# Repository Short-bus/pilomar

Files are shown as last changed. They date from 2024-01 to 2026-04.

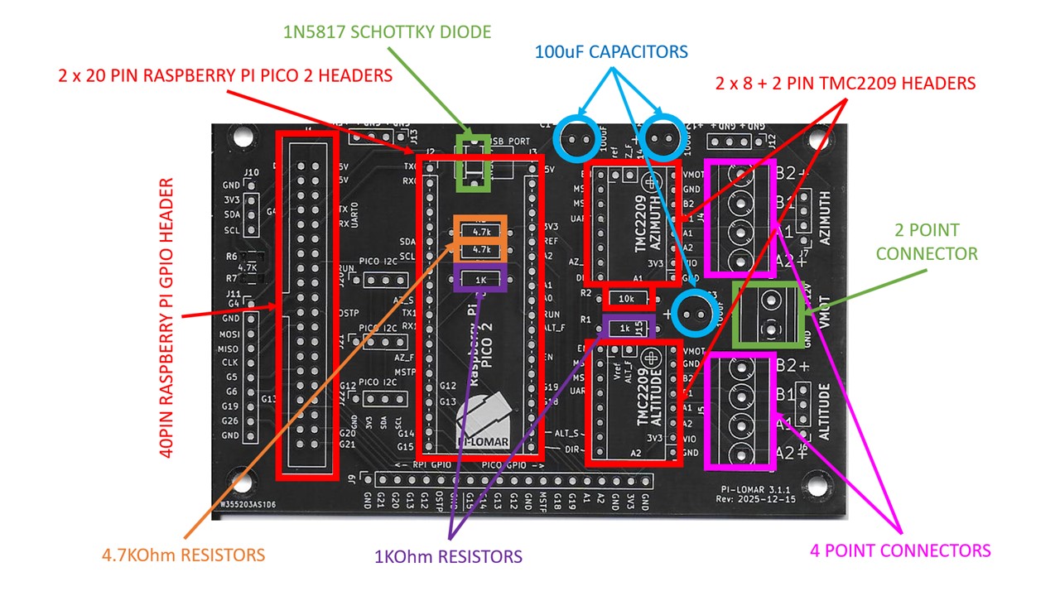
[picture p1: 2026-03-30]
gerber/PCB-2025-12-15/PCB GUIDE 2025-12-15.jpg

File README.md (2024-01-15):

# pi-lomar
RaspberryPi based miniature observatory.
A Python3 project to control a small camera and telephoto lens housed in a miniature 3D printed observatory enclosure.
This combines multiple open modules to handle object location, tracking and image capture.

This uses Python3 on the Raspberry Pi and CircuitPython on a connected Pimoroni Tiny2040 microcontroller.

The physical telescope, mechanism and dome is buildable from the Instructables page.
[https://www.instructables.com/Pi-lomar-3D-Printed-Working-Miniature-Observatory-/]

The wiki for pi-lomar is here.
[https://github.com/Short-bus/pilomar/wiki]

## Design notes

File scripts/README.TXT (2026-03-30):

This folder contains scripts for building the Pilomar project.

buildpilomar is the original (now deprecated build script).
buildpilomar_buster32 is the script to build on BUSTER O/S (for RPi3B and RPi4B).
buildpilomar_bookworm64 is the script to build on BOOKWORM O/S (for RPI4B and RPI5B).
zip-pilomar is a backup script. It archives the main programs and data files for pilomar.
astrometry.net will install the astrometry.net plate solving package on the RPi. It includes the asterism data files appropriate for the 16-50mm lenses used by the project.

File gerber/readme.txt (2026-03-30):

Each folder in the gerber directory is a complete Gerber file set for a single PCB design.

To send the Gerber files for manufacturing you should select the PCB version you want and ZIP all the files in that folder.
Eg:
  cd gerber/PCB-2023-12-14
  zip PCB-2023-12-14.zip *

Please order the board UNPOPULATED, the GERBER files do not specify the components, you need to add those manually when you 
have received the unpopulated PCBs.

These designs are made in good faith and are best efforts, but no guarantees are provided. 
Please be sure you are happy with their function and safety before using in your project.

PCB designs ----------------------------------------------------------------------------------------------------------------

PCB-2023-12-14 
  This is the initial PCB design for the motorcontrol board.
  Microcontroller: Pimoroni Tiny2040 and Tiny2350
  Stepper driver: DRV8815

PCB-2025-12-15
  This is the V3.1.1 version of the motorcontrol board.
  Microcontroller: Raspberry Pi Pico 2 (NOT PICO 1)
  Stepper driver: TMC2209 (Recommend Big Tree Tech V1.3)

Manufacturing settings -----------------------------------------------------------------------------------------------------

Board type : Single pieces
Different design in panel： 1
Size : 111.9 x 72.5 mm
Quantity :5
Layer : 2 Layers
Material :FR-4: TG130
Thickness : 1.6 mm
Min track/spacing : 8/8mil
Min hole size : 0.3mm ↑
Solder mask : Purple
Silkscreen : White
Edge connector : No
Surface finish : HASL with lead
"HASL" to "ENIG" : No
Via process : Tenting vias
Finished copper : 1 oz Cu
Remove product No. : No
Customized Services and Advanced Options : UL marking:None,

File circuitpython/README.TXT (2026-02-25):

This folder contains circuitpython code for the Pilomar project.

The tiny2040 subfolder contains the code.py program on the following setup:
    Pimoroni Tiny2040 microcontroller. 
    CircuitPython 7.2 to 8.2 only.
    drv8825 stepper motor drivers only.

The tiny2350 subfolder contains the code.py program on the following setup:
    Pimoroni Tiny2350 microcontroller. 
    CircuitPython 9.2 or later with RP2350 support.
    drv8825 stepper motor drivers only.

The pico2_tmc2209 subfolder contains the code.py program on the following setup:
    Raspberry Pi Pico2 microcontroller.
    CircuitPython 9.2 or later with Pico2 RP2350 support.
    tmc2209 stepper motor drivers only.

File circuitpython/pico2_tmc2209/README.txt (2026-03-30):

Files for:
   RASPBERRY PI PICO2 WITH TMC2209 STEPPER DRIVERS.
   These files are not designed to work on other microcontrollers or different stepper drivers.

This requires a circuit based upon the V3.1.1 motorcontroller because the microcontroller and stepper drivers have changed!

pi/circuitpython/pico2_tmc2209
│  
├─ README.txt # This file.
│  
├─ code.py # Primary program to run on Pico2 with tmc2209 stepper drivers.
│  
├─ tmc2209.py # Generic TMC Stepper library for communicating with tmc2209 stepper driver.
│  
├─ erase.py # Example code to erase file system on pico2 if a reset is needed.
│  
├─ as5600.py # Generic as5600 library for communicating with as5600 sensors.
│  
├─ pilomar # Pilomar project specific libraries.
│  │  
│  ├─ devices.py # Wrappers for sensors so they present common features to the project.
│  │  
│  ├─ enum.py # Used by some libraries.
│  │  
│  ├─ helpers.py # Misc functions and minor classes used by project.
│  │  
│  ├─ steppermotor.py # Main stepper motor class for the project.
│  │  
│  ├─ trajectory.py # Trajectory related classes for the project.
│  │  
│  └─ uarthost.py # UART serial communication handler for the project.
│
└─ lib # Adafruit libraries, included in project for convenience.
   │  
   ├─ adafruit_bus_device # Copy of adafruit_bus_device folder for convenience.
   │  
   ├─ adafruit_register # Copy of adafruit_register folder for convenience.
   │  
   └─ adafruit_lis3dh.mpy # Adafruit lis3dh handler included for convenience.

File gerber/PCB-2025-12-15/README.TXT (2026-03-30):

Gerber files to produce V3.1.1 PCB for the project.
This the newer PCB design which uses Raspberry Pi Pico2 microcontroller and TMC2209 stepper drivers.

You need to provide the following components to complete the board.
1 x 40 pin Raspberry Pi GPIO header.
2 x 20 pin headers for Raspberry Pi PICO2.
4 x 8 pin headers for TMC2209 drivers.
2 x 2 pin headers for TMC2209 drivers (NOTE: 2 extra pins along top edge of driver board).
2 x TMC2209 driver boards (recommend BigTreeTech V1.3 or equivalent).
1 x Raspberry Pi PICO2 microcontroller (NOTE: PICO1 does not work).
1 x 1N5817 Schottky diode.
2 x 4.7K resistors.
2 x 1.0K resistors.
1 x 10K resistor.
2 x 4 point terminal block.
1 x 2 point terminal block.
3 x 100uF Capacitors.

This requires software released from 2026 onwards. Earlier versions of Pilomar will not communicate correctly with this design.

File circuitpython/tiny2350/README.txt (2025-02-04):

This contains the circuitpython code for the Pimoroni Tiny2350 microcontroller.

To install:
1) Install CircuitPython on the Tiny2350. Version 9.2 works OK. Earlier versions do not support the Tiny2350 fully.
2) Copy code.py from this folder onto the Tiny2350.
3) Restart the Tiny2350.

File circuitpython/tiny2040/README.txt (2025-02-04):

This contains the circuitpython code for the Pimoroni Tiny2040 microcontroller.

To install:
1) Install CircuitPython on the Tiny2040. Versions 7.2 and 8.2 work OK. Later versions do not, they are too large.
2) Copy code.py from this folder onto the Tiny2040.
3) Restart the Tiny2040.

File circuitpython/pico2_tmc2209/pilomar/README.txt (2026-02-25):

circuitpython helper libraries for pico2 & tmc2209 support.

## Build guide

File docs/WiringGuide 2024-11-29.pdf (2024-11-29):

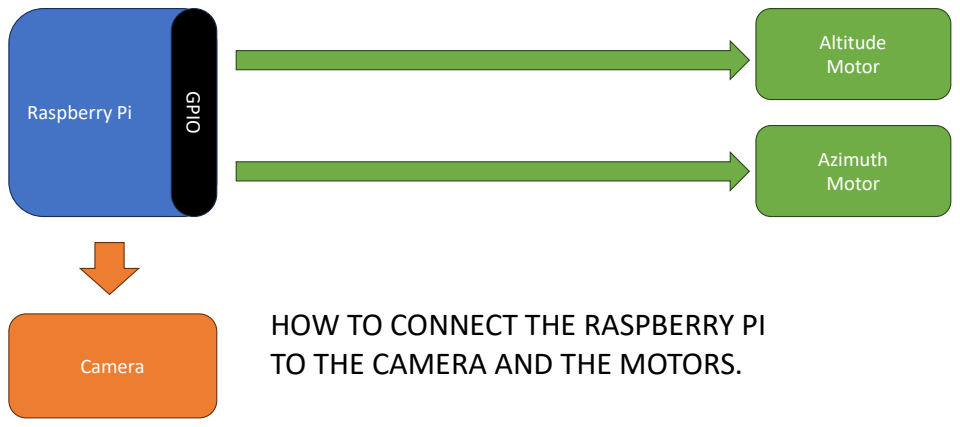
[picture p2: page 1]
Raspberry Pi; Altitude Motor; Camera; Azimuth; Motor GPIO

HOW TO CONNECT THE RASPBERRY PI
TO THE CAMERA AND THE MOTORS.

IDEALLY THE RASPBERRY PI WOULD
DIRECTLY CONTROL THE STEPPER
MOTORS THROUGH THE GPIO PORTS

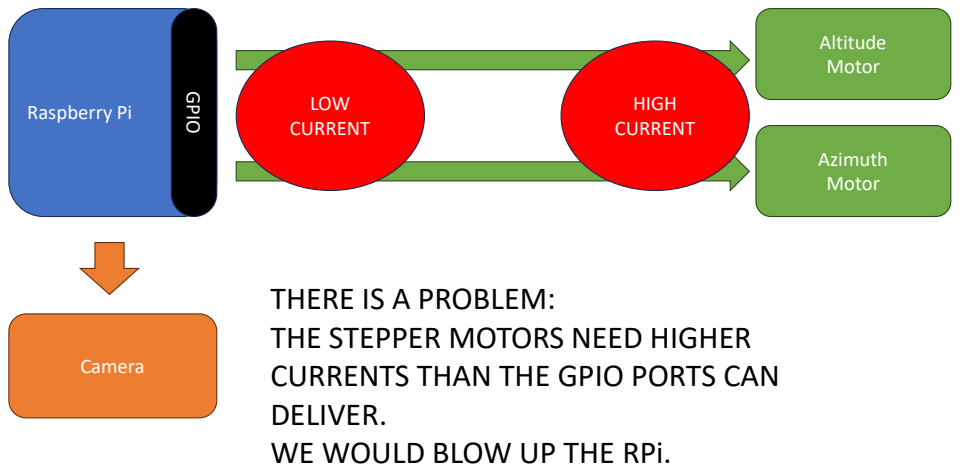
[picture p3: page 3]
Raspberry Pi; Altitude Motor; Camera; Azimuth; Motor GPIO; HIGH; CURRENT; LOW CURRENT

THERE IS A PROBLEM:
THE STEPPER MOTORS NEED HIGHER
CURRENTS THAN THE GPIO PORTS CAN
DELIVER.
WE WOULD BLOW UP THE RPi.

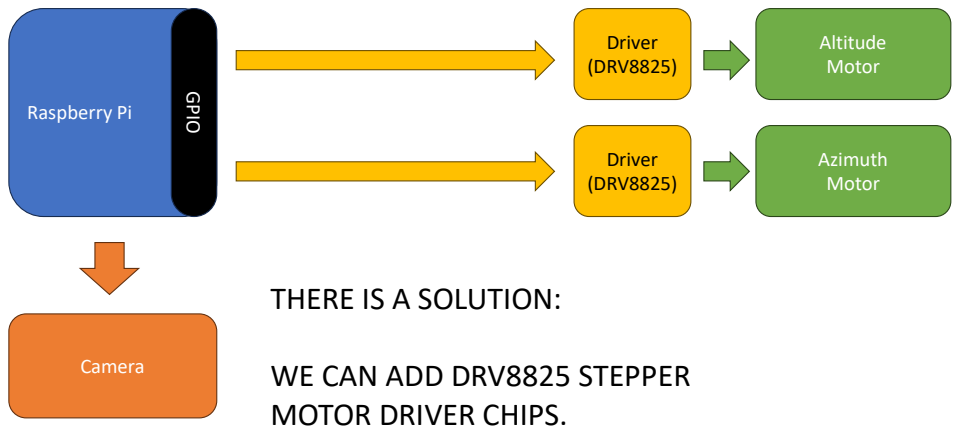
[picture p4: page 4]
Raspberry Pi; Altitude Motor; Camera; Driver (DRV8825); Azimuth Motor; Driver; (DRV8825) GPIO

THERE IS A SOLUTION:

WE CAN ADD DRV8825 STEPPER
MOTOR DRIVER CHIPS.

DRV8825 TAKES LOW POWER SIGNALS FROM
PROCESSORS TO CONTROL HIGHER
CURRENT/VOLTAGE POWER DIRECTLY TO THE
STEPPER MOTORS.

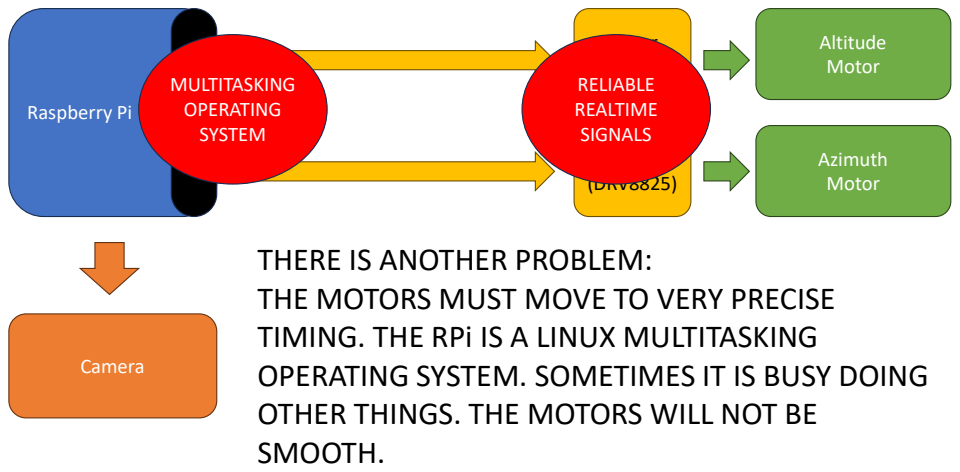
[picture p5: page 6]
Raspberry Pi; Altitude Motor; Camera; Driver (DRV8825); Azimuth Motor; Driver; (DRV8825) GPIO; RELIABLE REALTIME SIGNALS; MULTITASKING OPERATING SYSTEM

THERE IS ANOTHER PROBLEM:
THE MOTORS MUST MOVE TO VERY PRECISE
TIMING. THE RPi IS A LINUX MULTITASKING
OPERATING SYSTEM. SOMETIMES IT IS BUSY DOING
OTHER THINGS. THE MOTORS WILL NOT BE
SMOOTH.

THERE IS A SOLUTION:

INSERT A MICROCONTROLLER WHICH CAN PROVIDE
RELIABLE SIGNALS TO THE MOTORS. EVEN IF THE RPi
IS BUSY!

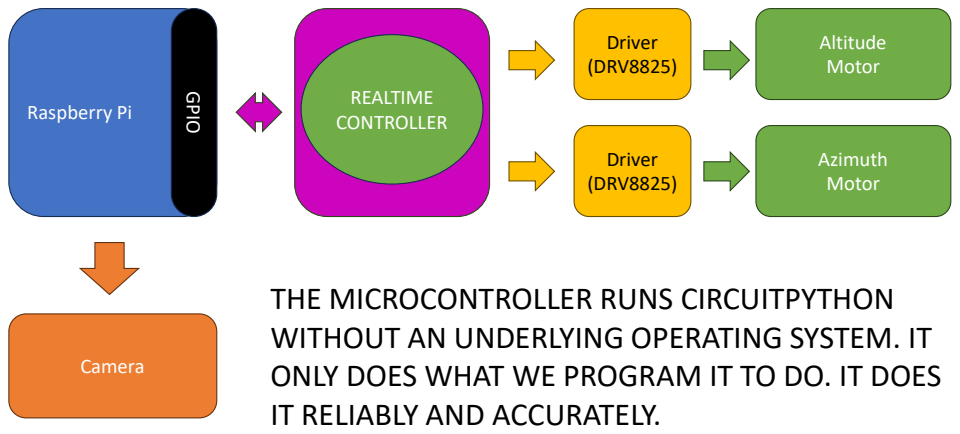
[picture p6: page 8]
Raspberry Pi; Altitude Motor; Camera; Driver (DRV8825); Microcontroller; Azimuth Motor; Driver; (DRV8825) GPIO; REALTIME; CONTROLLER

THE MICROCONTROLLER RUNS CIRCUITPYTHON
WITHOUT AN UNDERLYING OPERATING SYSTEM. IT
ONLY DOES WHAT WE PROGRAM IT TO DO. IT DOES
IT RELIABLY AND ACCURATELY.

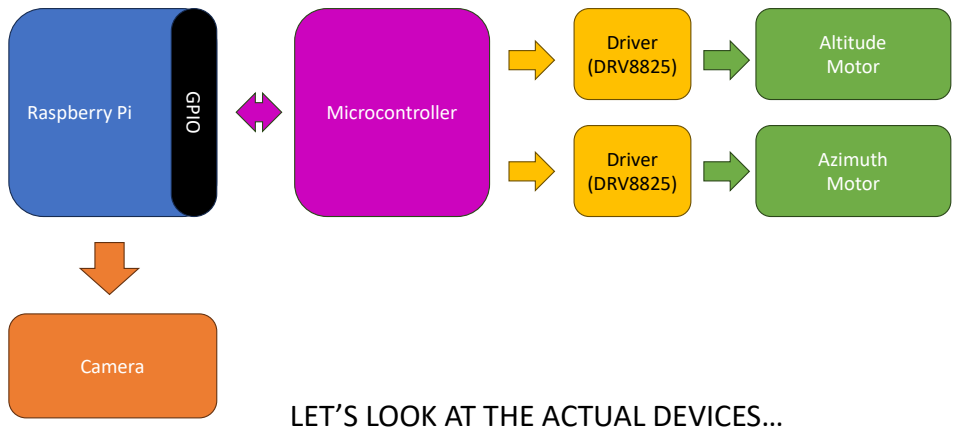
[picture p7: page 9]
Raspberry Pi; Altitude Motor; Camera; Driver (DRV8825); Microcontroller; Azimuth Motor; Driver; (DRV8825) GPIO

LET’S LOOK AT THE ACTUAL DEVICES…

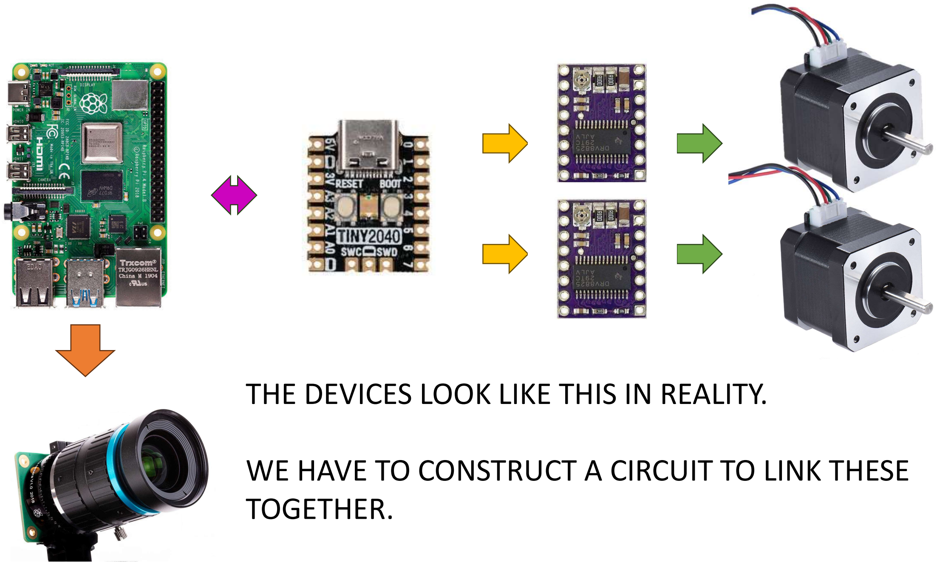
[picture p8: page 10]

THE DEVICES LOOK LIKE THIS IN REALITY.

# WE HAVE TO CONSTRUCT A CIRCUIT TO LINK THESE

TOGETHER.

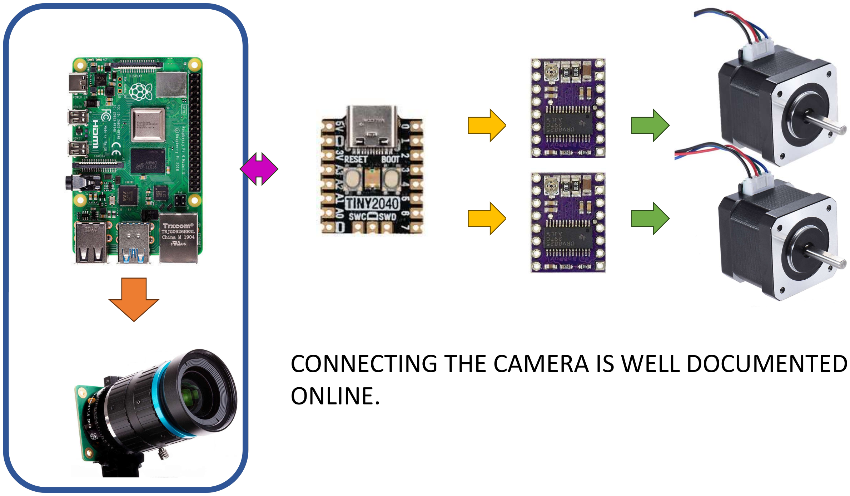
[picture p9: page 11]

# CONNECTING THE CAMERA IS WELL DOCUMENTED

ONLINE.

WE DON’T NEED TO DO ANYTHING SPECIAL WITH
THE CAMERA. JUST CONNECT IT AS EXPECTED.

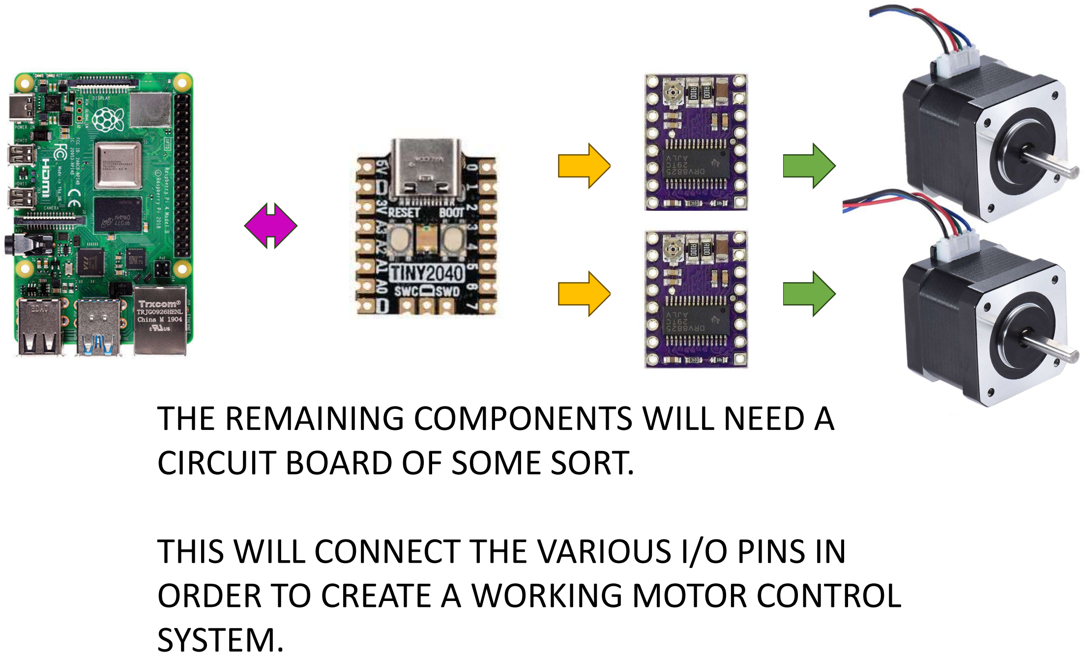
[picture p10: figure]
THE REMAINING COMPONENTS WILL NEED A CIRCUIT BOARD OF SOME SORT.; ORDER TO CREATE A WORKING MOTOR CONTROL SYSTEM.

# THIS WILL CONNECT THE VARIOUS I/O PINS IN

## RPI GPIO

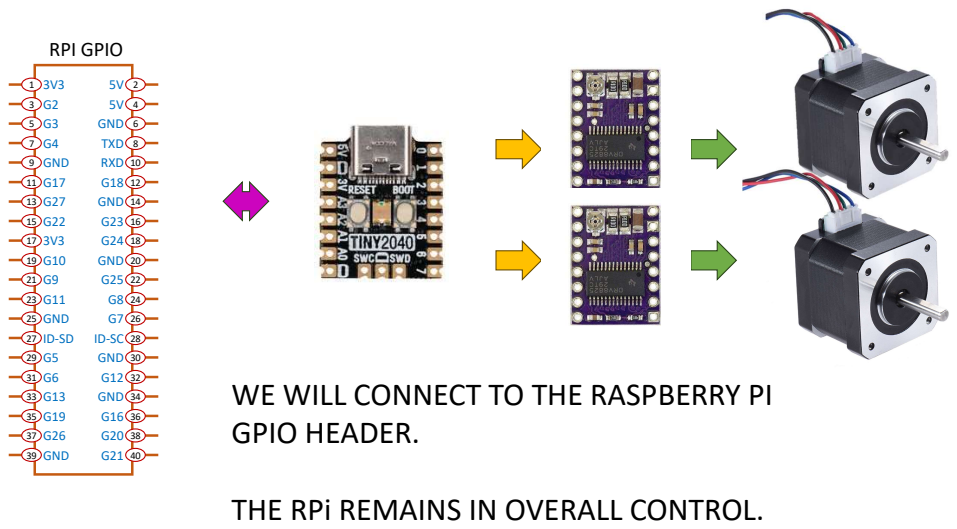
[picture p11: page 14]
5V 5V GND TXD RXD G18 GND G23 G24 GND; G8 G7 ID-SC GND G12 GND G16 G20 G21; 3V3 G2 G3 G4 GND G17 G27 G22 3V3 G10; G11 GND; G5 G6 G13 G19 G26 GND; WE WILL CONNECT TO THE RASPBERRY PI GPIO HEADER.; THE RPi REMAINS IN OVERALL CONTROL.

## TINY2040

## RPI GPIO

## TINY2040

# ID-SD ¹³⁵⁷⁹

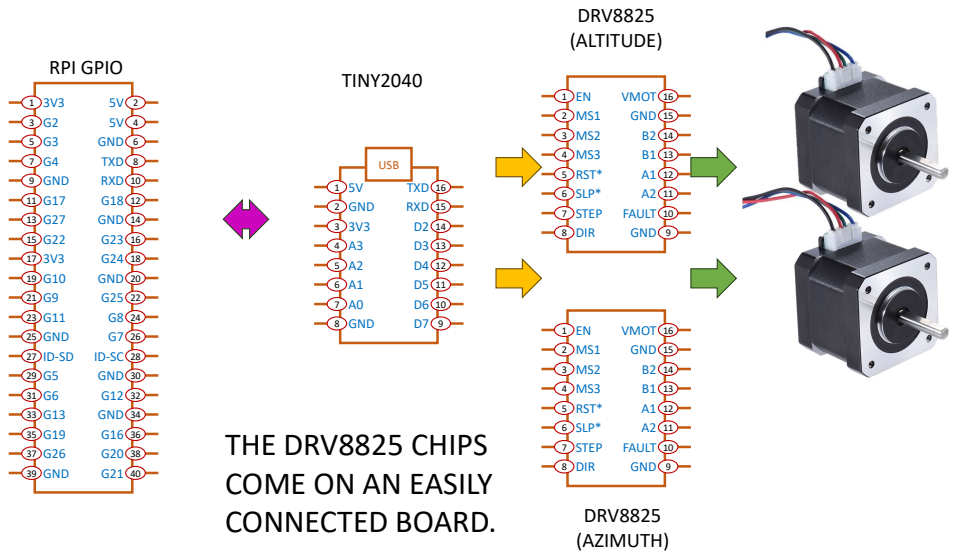
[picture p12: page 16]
5V 5V GND TXD RXD G18 GND G23 G24 GND; G8 G7 ID-SC GND G12 GND G16 G20 G21; 3V3 G2 G3 G4 GND G17 G27 G22 3V3 G10; G11 GND; G5 G6 G13 G19 G26 GND; TXD RXD D2 D3 D4 D5 D6 D7; 5V GND 3V3 A3 A2 A1 A0; GND ¹²³⁴⁵⁶⁷8; 11 109 VMOT; GND B2 B1 A1 A2 FAULT GND; EN MS1 MS2 MS3 RST* SLP* STEP; DIR ¹²³⁴⁵⁶⁷8; VMOT GND B2 B1 A1 A2 FAULT GND; DRV8825 (AZIMUTH); DRV8825 (ALTITUDE); RPI GPIO; THE DRV8825 CHIPS COME ON AN EASILY CONNECTED BOARD.; USB

## ALTITUDE

## DRV8825

## ALTITUDE

## DRV8825

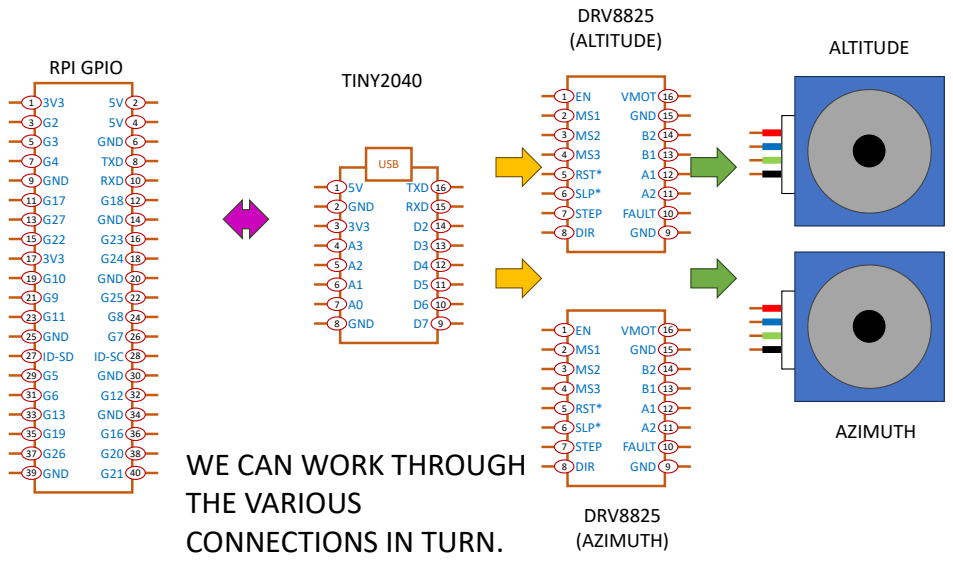
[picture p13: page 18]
AZIMUTH; DRV8825 (AZIMUTH); (ALTITUDE); TINY2040 RPI GPIO; 5V 5V GND TXD RXD G18 GND G23 G24 GND; G8 G7 ID-SC GND G12 GND G16 G20 G21; 3V3 G2 G3 G4 GND G17 G27 G22 3V3 G10; G11 GND; G5 G6 G13 G19 G26 GND; ID-SD ¹³⁵⁷⁹; TXD RXD D2 D3 D4 D5 D6 D7; 5V GND 3V3 A3 A2 A1 A0; GND ¹²³⁴⁵⁶⁷8; 11 109 VMOT; GND B2 B1 A1 A2 FAULT GND; EN MS1 MS2 MS3 RST* SLP* STEP; DIR ¹²³⁴⁵⁶⁷8; VMOT GND B2 B1 A1 A2 FAULT GND; WE CAN WORK THROUGH THE VARIOUS CONNECTIONS IN TURN.; USB

## ALTITUDE TINY2040 RPI GPIO

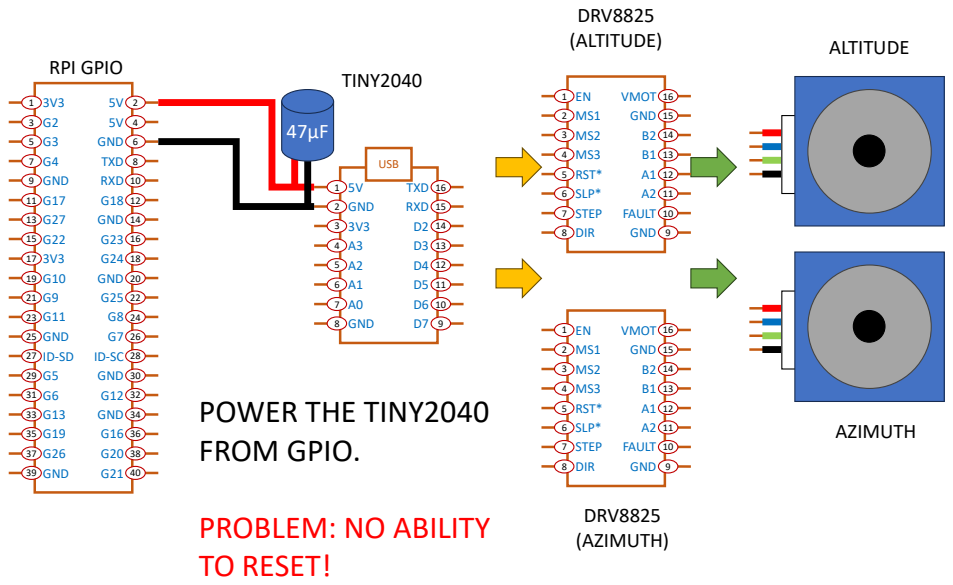
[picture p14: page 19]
AZIMUTH; 5V 5V GND TXD RXD G18 GND G23 G24 GND; G8 G7 ID-SC GND G12 GND G16 G20 G21; 3V3 G2 G3 G4 GND G17 G27 G22 3V3 G10; G11 GND; G5 G6 G13 G19 G26 GND; ID-SD ¹³⁵⁷⁹; TXD RXD D2 D3 D4 D5 D6 D7; 5V GND 3V3 A3 A2 A1 A0; GND ¹²³⁴⁵⁶⁷8; 11 109 VMOT; GND B2 B1 A1 A2 FAULT GND; EN MS1 MS2 MS3 RST* SLP* STEP; DIR ¹²³⁴⁵⁶⁷8; VMOT GND B2 B1 A1 A2 FAULT GND; POWER THE TINY2040 FROM GPIO.; PROBLEM: NO ABILITY TO RESET!; DRV8825 (AZIMUTH); DRV8825 (ALTITUDE); USB

## ALTITUDE TINY2040 RPI GPIO

## ALTITUDE TINY2040 RPI GPIO

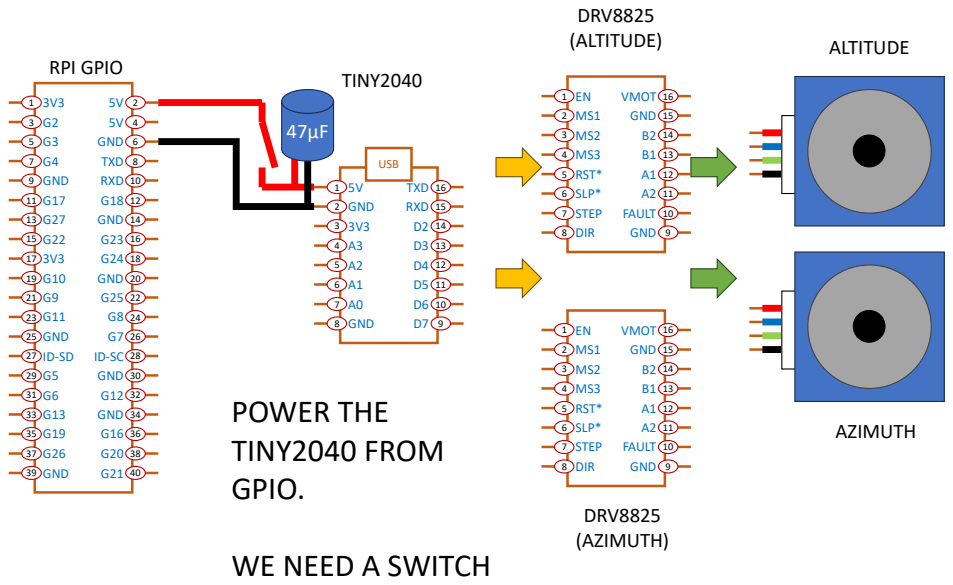
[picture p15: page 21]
AZIMUTH; 5V 5V GND TXD RXD G18 GND G23 G24 GND; G8 G7 ID-SC GND G12 GND G16 G20 G21; 3V3 G2 G3 G4 GND G17 G27 G22 3V3 G10; G11 GND; G5 G6 G13 G19 G26 GND; ID-SD ¹³⁵⁷⁹; TXD RXD D2 D3 D4 D5 D6 D7; 5V GND 3V3 A3 A2 A1 A0; GND ¹²³⁴⁵⁶⁷8; 11 109 VMOT; GND B2 B1 A1 A2 FAULT GND; EN MS1 MS2 MS3 RST* SLP* STEP; DIR ¹²³⁴⁵⁶⁷8; VMOT GND B2 B1 A1 A2 FAULT GND; POWER THE TINY2040 FROM GPIO.; DRV8825 (AZIMUTH); DRV8825 (ALTITUDE); USB

WE NEED A SWITCH

## ALTITUDE TINY2040 RPI GPIO

## ALTITUDE TINY2040 RPI GPIO

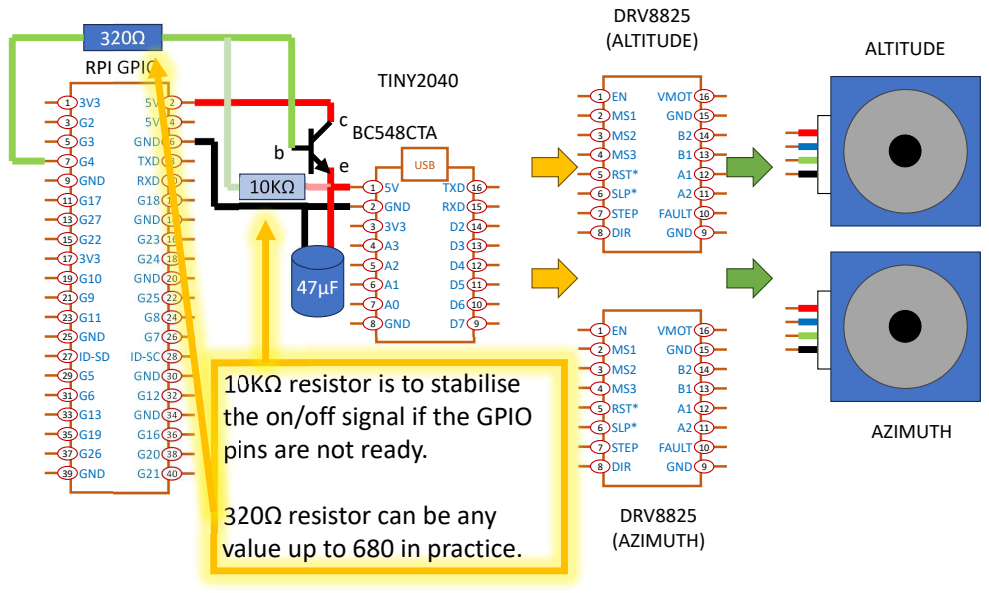
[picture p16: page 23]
AZIMUTH; 5V 5V GND TXD RXD G18 GND G23 G24 GND; G8 G7 ID-SC GND G12 GND G16 G20 G21; 3V3 G2 G3 G4 GND G17 G27 G22 3V3 G10; G11 GND; G5 G6 G13 G19 G26 GND; ID-SD ¹³⁵⁷⁹; TXD RXD D2 D3 D4 D5 D6 D7; 5V GND 3V3 A3 A2 A1 A0; GND ¹²³⁴⁵⁶⁷8; 11 109 VMOT; GND B2 B1 A1 A2 FAULT GND; EN MS1 MS2 MS3 RST* SLP* STEP; DIR ¹²³⁴⁵⁶⁷8; VMOT GND B2 B1 A1 A2 FAULT GND; BC548CTA; 10KΩ resistor is to stabilise the on/off signal if the GPIO pins are not ready.; 320Ω resistor can be any value up to 680 in practice.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

## ALTITUDE TINY2040 RPI GPIO

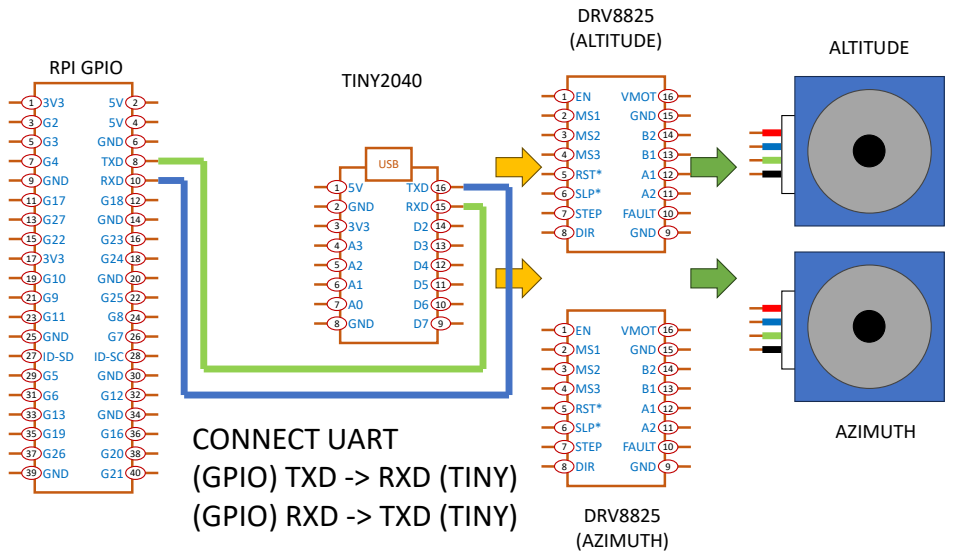
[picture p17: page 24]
AZIMUTH; 5V 5V GND TXD RXD G18 GND G23 G24 GND; G8 G7 ID-SC GND G12 GND G16 G20 G21; 3V3 G2 G3 G4 GND G17 G27 G22 3V3 G10; G11 GND; G5 G6 G13 G19 G26 GND; ID-SD ¹³⁵⁷⁹; TXD RXD D2 D3 D4 D5 D6 D7; 5V GND 3V3 A3 A2 A1 A0; GND ¹²³⁴⁵⁶⁷8; 11 109 VMOT; GND B2 B1 A1 A2 FAULT GND; EN MS1 MS2 MS3 RST* SLP* STEP; DIR ¹²³⁴⁵⁶⁷8; VMOT GND B2 B1 A1 A2 FAULT GND; CONNECT UART (GPIO) TXD -> RXD (TINY) (GPIO) RXD -> TXD (TINY); DRV8825 (ALTITUDE); DRV8825 (AZIMUTH); USB

## ALTITUDE TINY2040 RPI GPIO

## ALTITUDE TINY2040 RPI GPIO

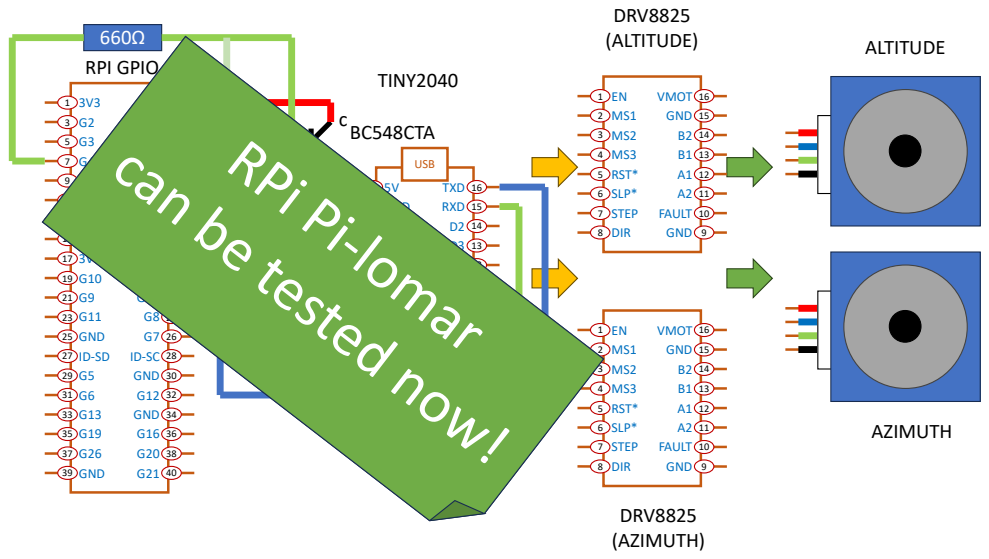
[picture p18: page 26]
AZIMUTH; 5V 5V GND TXD RXD G18 GND G23 G24 GND; G8 G7 ID-SC GND G12 GND G16 G20 G21; 3V3 G2 G3 G4 GND G17 G27 G22 3V3 G10; G11 GND; G5 G6 G13 G19 G26 GND; ID-SD ¹³⁵⁷⁹; TXD RXD D2 D3 D4 D5 D6 D7; 5V GND 3V3 A3 A2 A1 A0; GND ¹²³⁴⁵⁶⁷8; USB; VMOT GND B2 B1 A1 A2 FAULT GND; EN MS1 MS2 MS3 RST* SLP* STEP; DIR ¹²³⁴⁵⁶⁷8; DRV8825 (ALTITUDE); DRV8825 (AZIMUTH); BC548CTA

## ALTITUDE TINY2040 RPI GPIO

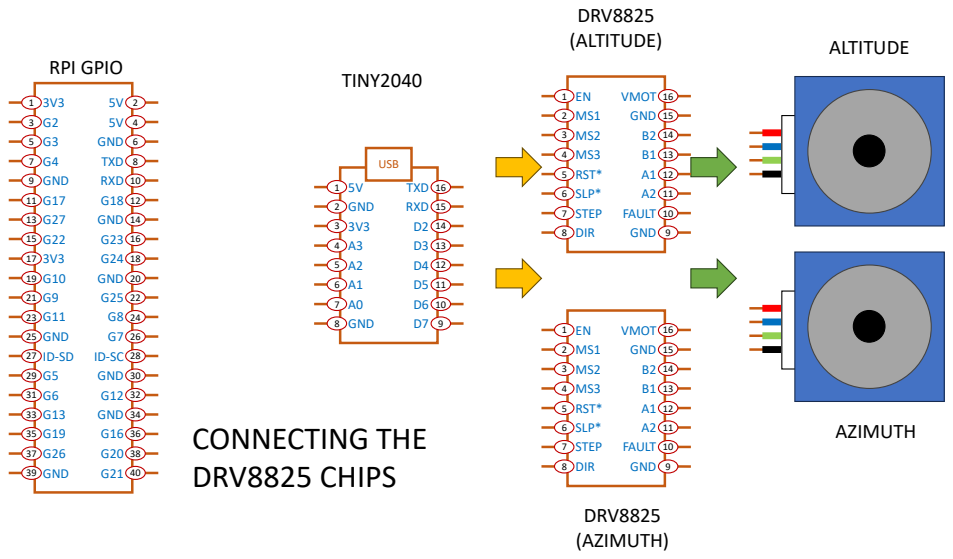
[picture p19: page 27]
AZIMUTH; 5V 5V GND TXD RXD G18 GND G23 G24 GND; G8 G7 ID-SC GND G12 GND G16 G20 G21; 3V3 G2 G3 G4 GND G17 G27 G22 3V3 G10; G11 GND; G5 G6 G13 G19 G26 GND; ID-SD ¹³⁵⁷⁹; TXD RXD D2 D3 D4 D5 D6 D7; 5V GND 3V3 A3 A2 A1 A0; GND ¹²³⁴⁵⁶⁷8; 11 109 VMOT; GND B2 B1 A1 A2 FAULT GND; EN MS1 MS2 MS3 RST* SLP* STEP; DIR ¹²³⁴⁵⁶⁷8; VMOT GND B2 B1 A1 A2 FAULT GND; DRV8825 (ALTITUDE); DRV8825 (AZIMUTH); CONNECTING THE DRV8825 CHIPS; USB

## ALTITUDE TINY2040 RPI GPIO

## ALTITUDE TINY2040 RPI GPIO

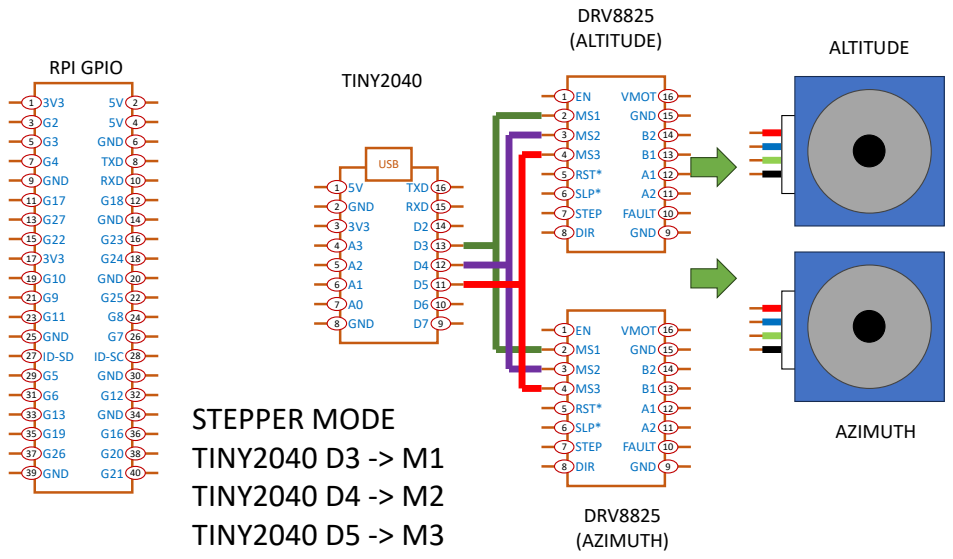
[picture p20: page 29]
AZIMUTH; 5V 5V GND TXD RXD G18 GND G23 G24 GND; G8 G7 ID-SC GND G12 GND G16 G20 G21; 3V3 G2 G3 G4 GND G17 G27 G22 3V3 G10; G11 GND; G5 G6 G13 G19 G26 GND; ID-SD ¹³⁵⁷⁹; TXD RXD D2 D3 D4 D5 D6 D7; 5V GND 3V3 A3 A2 A1 A0; GND ¹²³⁴⁵⁶⁷8; 11 109 VMOT; GND B2 B1 A1 A2 FAULT GND; EN MS1 MS2 MS3 RST* SLP* STEP; DIR ¹²³⁴⁵⁶⁷8; VMOT GND B2 B1 A1 A2 FAULT GND; DRV8825 (ALTITUDE); DRV8825 (AZIMUTH); STEPPER MODE TINY2040 D3 -> M1 TINY2040 D4 -> M2 TINY2040 D5 -> M3; USB

## ALTITUDE TINY2040 RPI GPIO

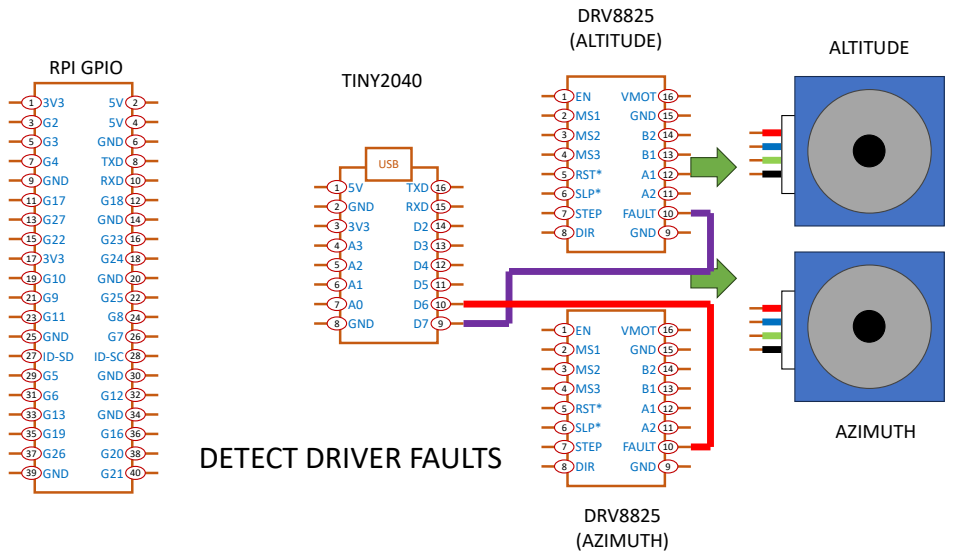
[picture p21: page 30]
AZIMUTH; 5V 5V GND TXD RXD G18 GND G23 G24 GND; G8 G7 ID-SC GND G12 GND G16 G20 G21; 3V3 G2 G3 G4 GND G17 G27 G22 3V3 G10; G11 GND; G5 G6 G13 G19 G26 GND; ID-SD ¹³⁵⁷⁹; TXD RXD D2 D3 D4 D5 D6 D7; 5V GND 3V3 A3 A2 A1 A0; GND ¹²³⁴⁵⁶⁷8; 11 109 VMOT; GND B2 B1 A1 A2 FAULT GND; EN MS1 MS2 MS3 RST* SLP* STEP; DIR ¹²³⁴⁵⁶⁷8; VMOT GND B2 B1 A1 A2 FAULT GND; DRV8825 (ALTITUDE); DRV8825 (AZIMUTH); DETECT DRIVER FAULTS; USB

## ALTITUDE TINY2040 RPI GPIO

## ALTITUDE TINY2040 RPI GPIO

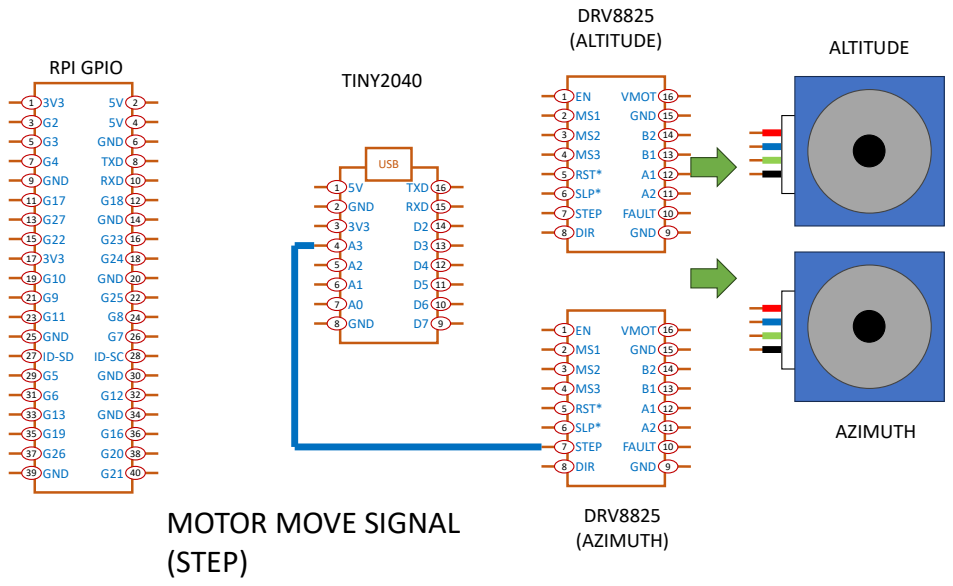
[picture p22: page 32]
AZIMUTH; 5V 5V GND TXD RXD G18 GND G23 G24 GND; G8 G7 ID-SC GND G12 GND G16 G20 G21; 3V3 G2 G3 G4 GND G17 G27 G22 3V3 G10; G11 GND; G5 G6 G13 G19 G26 GND; ID-SD ¹³⁵⁷⁹; TXD RXD D2 D3 D4 D5 D6 D7; 5V GND 3V3 A3 A2 A1 A0; GND ¹²³⁴⁵⁶⁷8; 11 109 VMOT; GND B2 B1 A1 A2 FAULT GND; EN MS1 MS2 MS3 RST* SLP* STEP; DIR ¹²³⁴⁵⁶⁷8; VMOT GND B2 B1 A1 A2 FAULT GND; DRV8825 (ALTITUDE); DRV8825; (AZIMUTH) MOTOR MOVE SIGNAL (STEP); USB

## ALTITUDE TINY2040 RPI GPIO

## ALTITUDE TINY2040 RPI GPIO

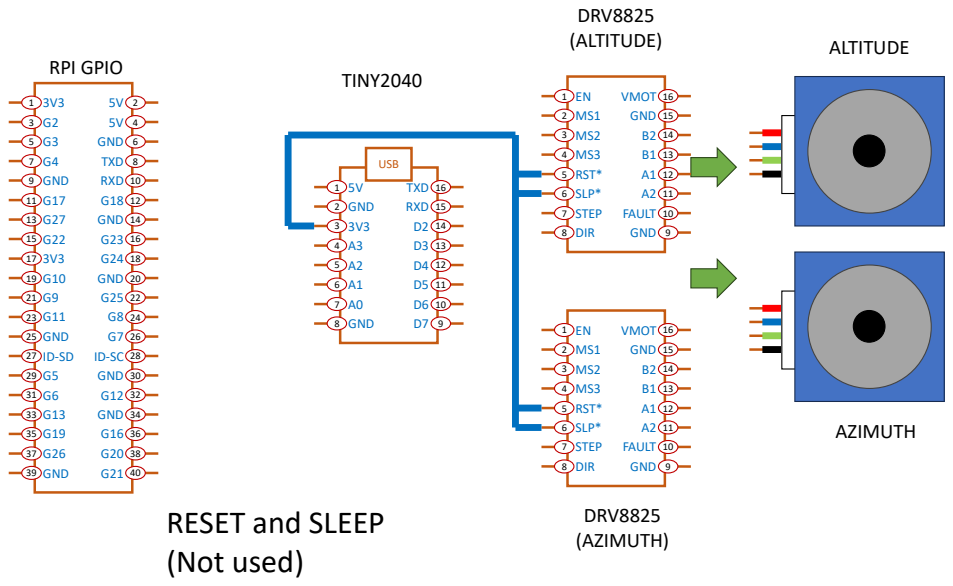
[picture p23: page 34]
AZIMUTH; 5V 5V GND TXD RXD G18 GND G23 G24 GND; G8 G7 ID-SC GND G12 GND G16 G20 G21; 3V3 G2 G3 G4 GND G17 G27 G22 3V3 G10; G11 GND; G5 G6 G13 G19 G26 GND; ID-SD ¹³⁵⁷⁹; TXD RXD D2 D3 D4 D5 D6 D7; 5V GND 3V3 A3 A2 A1 A0; GND ¹²³⁴⁵⁶⁷8; 11 109 VMOT; GND B2 B1 A1 A2 FAULT GND; EN MS1 MS2 MS3 RST* SLP* STEP; DIR ¹²³⁴⁵⁶⁷8; VMOT GND B2 B1 A1 A2 FAULT GND; DRV8825 (ALTITUDE); DRV8825; (AZIMUTH) RESET and SLEEP (Not used); USB

## ALTITUDE TINY2040 RPI GPIO

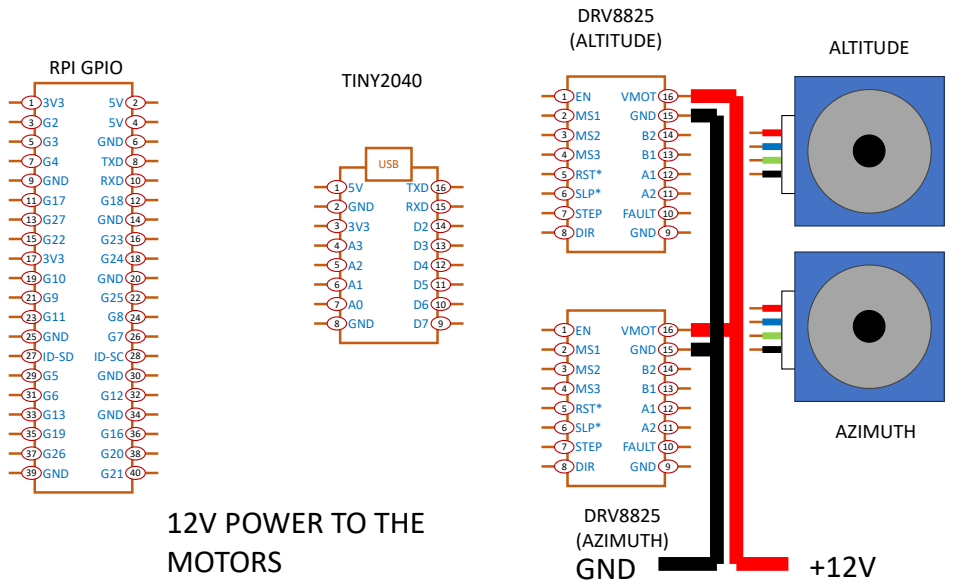
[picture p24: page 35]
AZIMUTH; 5V 5V GND TXD RXD G18 GND G23 G24 GND; G8 G7 ID-SC GND G12 GND G16 G20 G21; 3V3 G2 G3 G4 GND G17 G27 G22 3V3 G10; G11 GND; G5 G6 G13 G19 G26 GND; ID-SD ¹³⁵⁷⁹; TXD RXD D2 D3 D4 D5 D6 D7; 5V GND 3V3 A3 A2 A1 A0; GND ¹²³⁴⁵⁶⁷8; 11 109 VMOT; GND B2 B1 A1 A2 FAULT GND; EN MS1 MS2 MS3 RST* SLP* STEP; DIR ¹²³⁴⁵⁶⁷8; VMOT GND B2 B1 A1 A2 FAULT GND; DRV8825 (ALTITUDE); DRV8825; (AZIMUTH) 12V POWER TO THE; MOTORS; GND; USB

## ALTITUDE TINY2040 RPI GPIO

## ALTITUDE TINY2040 RPI GPIO

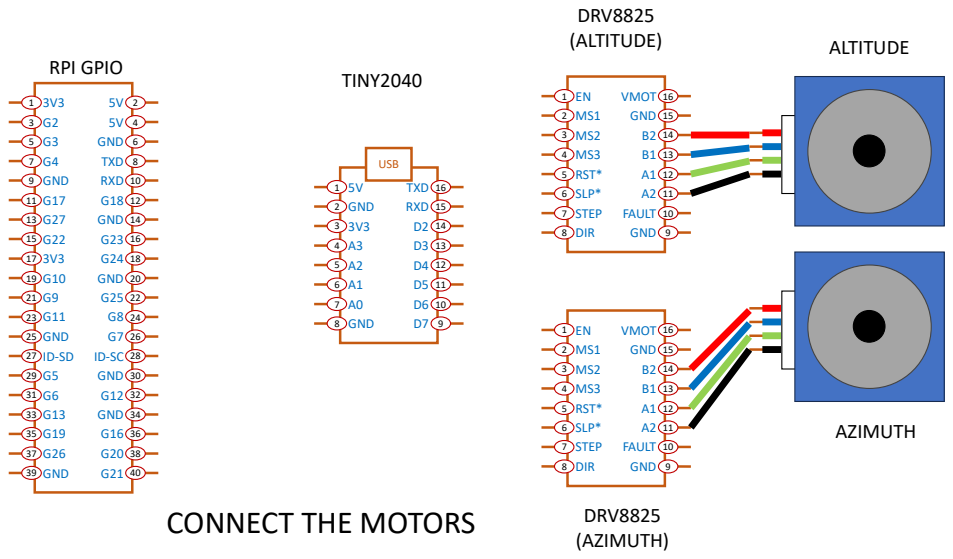
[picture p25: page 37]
AZIMUTH; 5V 5V GND TXD RXD G18 GND G23 G24 GND; G8 G7 ID-SC GND G12 GND G16 G20 G21; 3V3 G2 G3 G4 GND G17 G27 G22 3V3 G10; G11 GND; G5 G6 G13 G19 G26 GND; ID-SD ¹³⁵⁷⁹; TXD RXD D2 D3 D4 D5 D6 D7; 5V GND 3V3 A3 A2 A1 A0; GND ¹²³⁴⁵⁶⁷8; 11 109 VMOT; GND B2 B1 A1 A2 FAULT GND; EN MS1 MS2 MS3 RST* SLP* STEP; DIR ¹²³⁴⁵⁶⁷8; VMOT GND B2 B1 A1 A2 FAULT GND; DRV8825 (ALTITUDE); DRV8825; (AZIMUTH) CONNECT THE MOTORS; USB

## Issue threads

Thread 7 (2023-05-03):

Hi Quality camera board sometimes hangs

Short-bus, 2023-05-03:
Have seen rare occasions where the camera board hangs during a raspistill call.
The photograph capture begins, but never ends.
The software detects this and raises an error message, but so far no way to resolve the issue within the software.
Solution at the moment is to power cycle the whole raspberry pi to clear the problem.
Online search suggests this may sometimes occur if there is a power issue to the board.

Short-bus, 2024-02-05:
Witnessed the camera apparently hanging, this is the first time in months that it has happened.
Left the program to time out, it fails to shut down completely because the camerathread is still waiting for raspistill to return.
Instead of using <ctrl-c> to get the thread to terminate, I left it to run and see what happens.
After about 17 minutes the camera thread finally terminated by itself.
It appears that raspistill did eventually return control to the camerathread, but no idea why it took so long to capture the image.
The log file shows this 1046 second exposure, then the routine continues and terminates normally.
```
2024-02-05 18:48:45.643657+00:00	115.117265	astrocamera.CaptureSetFull(): Capture complete. ( 1046.07428 s).
2024-02-05 18:48:45.647283+00:00	0.000308	astrocamera.CaptureSetFull(): Load image from /media/pi/USBMEMORY/campaign_uranus_e10.0s/session_20240205181818/light/light_20240205183119_00.jpg
2024-02-05 18:48:45.650956+00:00	0.000068	pilomarimage camera .LoadFile( /media/pi/USBMEMORY/campaign_uranus_e10.0s/session_20240205181818/light/light_20240205183119_00.jpg )
2024-02-05 18:48:46.218098+00:00	0.563278	astrocamera.CaptureSetFull(): Image loaded.
2024-02-05 18:48:46.222966+00:00	0.000052	astrocamera.CaptureSetFull(): Converting to RAW (.DNG) file...
2024-02-05 18:48:47.740181+00:00	1.513554	astrocamera.CaptureSetFull(): Converted to RAW (.DNG) file.
2024-02-05 18:48:47.745066+00:00	0.000065	pilomarimage camera .SaveFile( /media/pi/USBMEMORY/campaign_uranus_e10.0s/session_20240205181818/light/light_20240205183119_00.jpg )
2024-02-05 18:48:48.323474+00:00	0.574238	astrocamera.CaptureSetFull(): Completed
2024-02-05 18:48:48.327252+00:00	0.000098	astrocamera.TakePhoto: Complete
2024-02-05 18:48:48.331752+00:00	0.000093	CameraHandler: End image capture
2024-02-05 18:48:48.335935+00:00	0.000103	CameraHandler: Total capture time 1048813.797ms. (mult= 104.8813797 )
2024-02-05 18:48:48.341235+00:00	0.000759	Folder for image details: /media/pi/USBMEMORY/campaign_uranus_e10.0s/session_20240205181818/
2024-02-05 18:48:48.374669+00:00	0.029583	pilomarimage camera .LineDetection()
2024-02-05 18:48:49.112723+00:00	0.733557	CameraHandler: Loop completed image in 1049.6 seconds
2024-02-05 18:48:49.117159+00:00	0.000118	CameraHandler: Completed loop 1345
2024-02-05 18:48:49.122025+00:00	0.000088	CameraHandler: TimeAllocation: image 1614.2388300000002 seconds ( 88 %)
2024-02-05 18:48:49.127320+00:00	0.000053	CameraHandler: TimeAllocation: pause 86.35953700000002 seconds ( 4 %)
2024-02-05 18:48:49.132888+00:00	0.000049	CameraHandler: TimeAllocation: preview 31.153741999999998 seconds ( 1 %)
2024-02-05 18:48:49.136913+00:00	0.000059	CameraHandler: TimeAllocation: tracking 90.38564799999999 seconds ( 4 %)
2024-02-05 18:48:49.142995+00:00	0.000080	CameraHandler: Parent thread is nolonger alive. Terminating
2024-02-05 18:48:54.154757+00:00	5.006073	CameraHandler: Finished.

```

Short-bus, 2024-11-22:
Closed as there are no plans/ideas for this.

Closed 2024-11-22.

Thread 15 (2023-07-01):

Optimistic configuration

Short-bus, 2023-07-01:
Whenever the microcontroller restarts it needs a new configuration and trajectory.
The current solution is 'pessimistic', always assuming that the microcontroller can reset at any moment.
The pimoroni Tiny2040 microcontroller has proven much more reliable, so it's possible to be more optimistic and send a larger packet of trajectory elements at the start of the observation. This would speed up the initialisation of an observation.
Can an 'optimistic' startup option be added easily?

Closed 2024-08-01.

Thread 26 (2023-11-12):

When exercising the altitude motor, there is sometimes a 'dip' before elevating the camera - why?

Short-bus, 2023-11-12:
While exercising the altitude motor I noticed that sometimes the camera 'dips' before raising to the assigned altitude. It appears to be a deliberate movement of the motors, but is unexpected. Needs to be investigated. This behaviour hasn't been witnessed on the azimuth motor - which should be processed identically in the software. Is this a bug or something else?

Short-bus, 2024-01-21:
circuitpython/code.py has a default 'BacklashAngle' of 0.5 degrees for the Azimuth motor, which is not required in the current build. However the Altitude motor already defaults to '0.0' degrees. So backlash handling does not appear to be the cause.

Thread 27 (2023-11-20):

Custom PCB Procurement

baqwas, 2023-11-20:
Is the custom PCB available for _cloning_ for use by others? Would like to order one from PCBway if you approve!

Also, is there a full schematic of all the connections in any other document? It is next to impossible to _read_ the schematic in the PDF document. Thanks.

Regards.

baqwas, 2023-11-20:
Thanks for the quick update, @Short-bus. Not an issue with the PCB situation.

I simply wanted to understand the advantage of the RP2040 (any model) because I've been driving **gimbal** movements with _hobbyist_ servo motors and one Arducam PTZ setup using several different SBCs without an intermediate hop - all with motor power supply isolated.

Haven't fully digested your notes on the advantages of the RP2040 (+ specifically the Pimoroni model) but your recommendations are to avoid driving the servos directly from the RPi (even with _totally separate power supply_ to the servos), I believe. Thanks again.

Regards.

Closed 2023-11-20.

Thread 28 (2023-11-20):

Raspbian Buster (Debian 10) image nolonger on main Raspberry Pi downloads page

Short-bus, 2023-11-20:
The launch of the latest Raspbian version has pushed Buster off the list of legacy O/S images on the Raspberry Pi website.
The Instructables page lists a version date that is nolonger visible anywhere.
Raspberrypi.org website has an archive of all older O/S versions - so there should be a suitable Buster image available there.
The latest image is from 2021-05-07.
Does the build script install all requirements on this version or is anything additional required?

Short-bus, 2023-11-28:
Currently testing build with available 2021-05-07 release.

Short-bus, 2023-11-29:
Fresh build from scratch on 2021-05-07 release appears to be compatible with the version originally available from the RPi OS imager.

Closed 2023-11-29.

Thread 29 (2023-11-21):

Instructables link in README.md points to GitHub

kf6spf, 2023-11-21:
Hi ...

The link at the bottom of the README file:

`The physical telescope, mechanism and dome is buildable from the Instructables page. [https://github.com/Short-bus/pilomar]`

... points back to GitHub instead of the Instructables page:

[https://www.instructables.com/Pi-lomar-3D-Printed-Working-Miniature-Observatory-/](https://www.instructables.com/Pi-lomar-3D-Printed-Working-Miniature-Observatory-/)

Short-bus, 2023-11-21:
Thanks. Changed the link as you suggested.

Closed 2023-11-21.

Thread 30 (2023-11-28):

When closing down pi-lomar on a fresh build, error trying to write non-existent MotorRunningSeconds to recovery file.

Short-bus, 2023-11-28:
Code from experimental feature still in the released version.
The program is trying to write MotorRunningSeconds value for each motor to the position recovery file.
This causes the program to loop with the same error when trying to shut down.
Remove the rogue references to MotorRunningSeconds and related motor running time calculations.

Short-bus, 2023-11-29:
Removed references to MotorRunningSeconds.
Also fixed potential permanent looping if writing to recoveryfile failed due to missing attributes.

Closed 2023-11-29.

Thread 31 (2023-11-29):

MarkupPreview throws Pandas error if 'knownas' column is not available.

Short-bus, 2023-11-29:
09:19:47 Begin preview image generation.
Exception in thread Thread-2:
Traceback (most recent call last):
  File "/usr/local/lib/python3.7/dist-packages/pandas/core/indexes/base.py", line 3361, in get_loc
    return self._engine.get_loc(casted_key)
  File "pandas/_libs/index.pyx", line 76, in pandas._libs.index.IndexEngine.get_loc
  File "pandas/_libs/index.pyx", line 108, in pandas._libs.index.IndexEngine.get_loc
  File "pandas/_libs/hashtable_class_helper.pxi", line 5198, in pandas._libs.hashtable.PyObjectHashTable.get_item
  File "pandas/_libs/hashtable_class_helper.pxi", line 5206, in pandas._libs.hashtable.PyObjectHashTable.get_item
KeyError: 'knownas'

Column is not available in the data for this version of the program.
Field reference needs to be removed.

Short-bus, 2023-11-29:
pilomar.py is now tolerant of the missing column.
Updated ngc.json to include the latest columns.

Short-bus, 2023-11-29:
Closed.

Closed 2023-11-29.

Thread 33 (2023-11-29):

Can src/pilomar.py run without the microcontroller at all?

Short-bus, 2023-11-29:
Currently src/pilomar.py on the RPi needs to communicate with the microcontroller on the motorcontrol board if the software is to successfully run.
Is it viable to have the RPi side run with no microcontroller connected at all?
Does it require a simulator for the microcontroller, or is there a simple way to disable the communication and still have the RPi continue as if a microcontroller was communicating?
The RPi side would need to update some information as if the microcontroller was present otherwise it consider that the communication and motion is failing.

Short-bus, 2024-11-22:
Closed as no further action planned on this one.

Closed 2024-11-22.

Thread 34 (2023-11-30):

Add parameters for star selection magnitude for star lists.

Short-bus, 2023-11-30:
LocalStars and ConstellationStars lists of stars use hardcoded magnitude filter.
This needs to change if different focal length lenses are chosen.
Turn both magnitude values into parameters so it is more clear what to change.
Magnitude 9 is a good value for 50mm lenses.
Magnitude 7 is better for 16mm lenses.

Short-bus, 2023-11-30:
Testing the 2 new parameters this week before committing the change.

Short-bus, 2023-12-28:
Added a new utility function "TrackingStatus()" on the Miscellaneous Tools Menu to show the tracking parameters in use.

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

It's likely that individual telescopes will want to tune the parameters for the tracking system depending upon their skies.
The new utility lists the relevant parameters and suggests how to adjust star counts.
This is likely to evolve as it is tested more.

Closed 2023-12-30.

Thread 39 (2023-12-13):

After building the Hipparcos star catalog, pilomar terminates at target prompt

Short-bus, 2023-12-13:
If pilomar has to build the Hipparcos start catalog when first installed it sometimes fails when the first user input is requested.
After successfully completing the catalog build it asks for a target to be selected, but the prompt fails with an IO error.

Restarting the program solves the problem.

The catalog build takes a long time and something with the user IO seems to timeout during that period.

Is it better to have a clean shutdown after building the catalog and asking the user to restart the program anyway?

Short-bus, 2023-12-18:
Until the root cause is identified the program will terminate more cleanly after constructing the Hipparcos catalog.

Short-bus, 2023-12-20:
Recreated the error condition

Menu option : Traceback (most recent call last):
  File "pilomar.py", line 6358, in <module>
    Session.Target = TargetSelection()
  File "pilomar.py", line 6318, in TargetSelection
    option = TargetMenu.Prompt() # As the user to select an option from the menu.
  File "/home/pi/pilomar/src/textcolor.py", line 2547, in Prompt
    answer = input(textcolor.cyan('Menu option : ')) # Prompt for input.
ValueError: I/O operation on closed file.
pi@pilomar3b:~/pilomar/src $

Does the routine that reads the downloaded data close the terminal I/O somehow?

Short-bus, 2023-12-21:
Code which performs the Hipparcos catalog build...

from skyfield.api import Loader # Create own 'load' functionality by specifying the download directory this way.
...
load = Loader(ProjectRoot + '/data') # Create own version of Skyfield 'load' object. This version saves cache files in the data directory.
...
    with load.open(HipparcosUrl,reload=ReloadData) as f: # load function will use disc cache if it already exists.
        HipparcosDf = hipex_load_dataframe(f) # Hipparcos data as a Pandas dataframe.
        MainLog.Log('Hipparcos data:',list(HipparcosDf.columns),terminal=False)
        MainLog.Log("Saving Hipparcos cache as",HipparcosCacheFile,terminal=True)
        HipparcosDf.to_pickle(HipparcosCacheFile)

Simple experiment with the pandas.to_pickle() function did not cause any problems for follow-on input() statement.

Short-bus, 2024-01-17:
Found this reference to a similar situation online...
https://stackoverflow.com/questions/50751103/i-o-operation-on-closed-file-using-input

The discussion suggests that one possibility is an 'exit()' statement buried in some other library, this could close the sys.stdin files. The same error message appeared elsewhere in the program during testing, that may also be an exit() statement in an included procedure.

Short-bus, 2024-02-27:
Have now seen the same error message occur at other prompts a couple of times, it appears to happen if the program is left unattended for a long time. Could it be related to the VNC connection?

Closed 2025-04-20.

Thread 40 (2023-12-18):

Code.py UART TX buffer can overflow if DRV8825 fault, but FaultSensitive=False

Short-bus, 2023-12-18:
If the Tiny2040 is receives a 'fault' signal from a DRV8825 board AND the parameter FaultSensitive = False a crash can occur.
Crash is caused by repeated log messages about the fault pin.
FaultSensitive=True will cause the routine to quit immediately,
But FaultSensitive=False will allow it to continue and keep raising the error with each step.
This condition can occur if FaultSensitive=False and the Tiny2040 is not physically wired up to a DRV8825.
Found during PCB testing.
The Fault pin on the Tiny2040 must float 'low' in this situation and trigger the fault condition.
The FaultSensitive parameter was a recent addition, situation could not occur in earlier versions.

Short-bus, 2023-12-18:
Introduced latch so that the error message is only generated a single time.
Scenario that caused original fault now passes OK.

Short-bus, 2023-12-18:
In 2023-Dec-issues branch.

Closed 2023-12-30.

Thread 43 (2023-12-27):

Local timezone setting can be made simpler.

Short-bus, 2023-12-27:
The parameter file contains a local timezone parameter. (LocalTZ)
This defaults to 'Europe/London'. It is available for information and if you want to adapt the software further.
The program works almost exclusively in UTC times at the moment.
You can get the current UTC time with the NowUTC() function.
You can get the current LOCAL time with the UTCtoLocal() function.
Eg:
print("local time is",UTCtoLocal(NowUTC()))
If you want to use this function you need to select the correct local timezone value for the parameter file.
The list of valid codes is available online, but you can also get it from the pytz package itself.
In Python

>>> import pytz
>>> print(pytz.all_timezones)

You can set the parameter to any of the values listed there.

pilomar has a useful 'listchooser' function which can be used to make this parameter setting simpler.
This is a low priority issue, but easy to implement.

Short-bus, 2024-11-22:
Later note: Some additional protection added into LoadParameters() method so that bad values are recognised and reset to something safe.
Previous release already added the ability to choose a good LocalTZ value via the Miscellaneous tools menu.

Closed 2023-12-30.

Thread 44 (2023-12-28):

Issues related to CircuitPython 8.x installation on Tiny2040

Short-bus, 2023-12-28:
Current recommendation is CircuitPython 7.2.0 installation.
Later versions have not been validated.
When trying to run CircuitPython 8.x some items appeared.

- The busio.UART.read(1) method nolonger works. It fails because the nbytes parameter is not specifically named. busio.UART.read(nbytes=1) may solve this. It needs testing. I found a reference online that the underlying MicroPython and libraries changed sometime after 7.2.0 and now requires some busio.UART parameters to be named.
- The error messages from the uarthost class can be standardised in line with the rest of the programs. Making the source of errors more clear.
- At boot the boot_out.txt file could be passed back to the RPi to aid with problem solving. That will show what type and version of python is installed on the microcontroller.
- Also noticed that the recommended CircuitPython uf2 filename in the archive is now different from the original documentation, the file and date appear to be the same, but the filename has subtly changed. Update the instructions.

Short-bus, 2023-12-30:
Tested busio.UART.read(nbytes=1) on circuitpython 7.2.0, this generates an error. So have not futureproofed the function call yet.
Have left a comment in the code instead to warn that the busio.UART.read() call must change depending upon the circuitpython version.

Also changed the initialization color on the microcontroller from PINK 5 seconds, to CYAN 3 seconds. PINK is too close to the RED error color and it does not need to be displayed for very long.

Short-bus, 2024-02-25:
circuitpython/code.py in the 2024-01-issues branch now successfully runs on the latest CircuitPython stable release for the Tiny2040.
`Adafruit CircuitPython 8.2.10 on 2024-02-14; Pimoroni Tiny 2040 (8MB) with rp2040`
The busio.UART.read(nbytes=1) error was misleading, the fault was elsewhere.
The program now uses a slightly different method to initialize the UART comms and to perform the read.
For CircuitPython7.2 the old code remains in use to reduce the risk of disturbing existing installations. The program chooses which solution to use at launch depending upon the CircuitPython version identified in the boot_out.txt file. Any version BEFORE 8.0 uses the original solution. Any version from 8.0 onwards uses the new solution.

Short-bus, 2024-02-27:
Done.

Closed 2024-02-27.

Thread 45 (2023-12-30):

Preparations for PCB design

Short-bus, 2023-12-30:
Testing 2 PCB designs.

- "Ton's design"
- "Rev 2023-12-14"

Any software issues related to the PCB functionality can be gathered here.

Both PCB designs release the ADC0 pin on the Tiny2040 microcontroller, the software should support that being reallocated as a general purpose IO pin.

"Rev 2023-12-14" board exposes more of the RPi GPIO pins for other purposes (GP12, GP13, GP16, GP19, GP20, GP26, SCL, SDA and 3V3). Check for any conflicts.

Closed 2025-04-18.

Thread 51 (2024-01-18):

Preview can inherit previous target as background.

Short-bus, 2024-01-18:
When selecting 2nd and subsequent targets the preview function can inherit the previous target's image as the background.
This happens only if the 'preview' function triggers BEFORE a live image has been captured of the current target.
At the start of the observation the image buffers should be reset.

Short-bus, 2024-01-27:
2024-01-issues branch should address this.

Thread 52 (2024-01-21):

Move more motor parameters into parameter file.

Short-bus, 2024-01-21:
Some motor parameters are currently hardcoded. The same values must be maintained in src/pilomar.py and circuitpython/code.py if a build uses different motors or modifies the drive mechanism.
If the software is then updated, any locally changed values will be replaced with the master copy values.
Take more of the motor settings from the parameter file so that there is a single point to define them and they are retained across software versions.

Add GearRatio, MotorStepsPerRev, MicrostepRatio and RestAngle to the 'configure motor' message.

Short-bus, 2024-01-27:
2024-01-issues branch has these changes in place.

Short-bus, 2024-02-27:
Done.

Closed 2024-02-27.

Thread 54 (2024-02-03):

Tree branches confuse astroalign

Short-bus, 2024-02-03:
The attached images show a case where there are trees in the field of view and it seems to confuse the astroalign routine.
The branches are being recognised as potential stars.
As a workaround have suggested trying shorter exposure times in TrackingExposureSeconds, reducing from 5 seconds to 1 or 2 seconds to see if a darker image helps the real stars stand out better in the image.

**Original Tracking_Analysis image**
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

**Original Latest_Tracking image**
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

**Original Target_Tracking image**
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

Short-bus, 2024-02-04:
Adding experimental new parameter "TrackingUrbanFilter".
Default (False) - means no effect.
When set to True, the program uses OpenCV to try to remove 'haze' from the image.
It also reduces the impact of tree branches in the image.

The filter blurs the image horizontally to establish a background light level for the image.
This blurred image is subtracted from the live captured image.
The result is then passed to the pilomarimage.EnhanceStars() method.
EnhanceStars() applies OpenCV's Gaussian Blur and Threshold methods to isolate the stars that remain.

Needs to be tested and tuned with more observations.

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

Short-bus, 2024-02-27:
2024-01-issues has a workaround in the new filter scripts, these can be further adjusted now via the parameter file.

Closed 2024-02-27.

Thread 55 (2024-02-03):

Motors do not configure but UART OK.

Short-bus, 2024-02-03:
There's a case where the UART communication log on the RPi looks OK.
There are SEND and RECEIVE messages being logged between the RPi and the microcontroller.
However the messages coming back from the microcontroller suggest that the RPi messages are not being handled properly by the microcontroller.
eg: Motor configurations are sent, but the returned motor status does not show that the configuration has been set.
eg: The 'set time' message is sent to the microcontroller, but the microcontroller messages do not show the synchronised time in the example messages seen.
Is there a way to identify what is causing the problem?

Full log file probably needs checking for other error messages.
Microcontroller could be hooked up to UART & USB so it can be monitored through the SHELL window in Thonny.

Original message:
```
Troubleshooting help

 'Motor Tools' > 'Tune Azimuth' > '1000' > Enter

motorcontroller.TunePosition( azimuth ): Motor is not yet configured. Tune command will not be sent.

Tiny 2040 LED does light up prior to running the adjustment.

Motors do not move at all

Checked soldering, no change, can anybody cypher the log?
```

```
received:   motor status 20200101000016 azimuth n 20200101000016 0 48000 180.0 n n 0.1 2464 tmr
queueing   (Q# 1): configure motor 20240203171249 azimuth 180.0 0 360 0.0 -1 0.001 0.05 0.003 10 [14]
received:   motor status 20200101000016 altitude n 20200101000016 000.0nn0.1 3024 tmr
queueing   (Q# 2): configure motor 20240203171249 altitude 0.0 0 90 0.0 -1 0.001 0.05 0.003 10 [15]
received:   log :20200101000017:CPU UID: df-60-9c-80-67-2b-45-28 Core: 0, ResetReason: POWER_ON, Temp:   -92.2365, Freq: 125M, Volt:   3.3
received:   log :20200101000017:CPU UID: df-60-9c-80-67-2b-45-28 Core: 1, ResetReason: POWER_ON, Temp:   -92.7046, Freq: 125M, volt:   3.3
queueing   (Q# 1): # heartbeat [16]
received:   motor status 20200101000026 azimuth n 20200101000026 0 48000 180.0 n n 0.1 2400 tmr
queueing   (Q# 1): configure motor 20240203171259 azimuth 180.0 0 360 0.0 -1 0.001 0.05 0.003 10 [17]
received:   motor status 20200101000026 altitude n 20200101000026 000.0nn0.1 2992 tmr
queueing   (Q# 2): configure motor 20240203171259 altitude 0.0 0 90 0.0 -1 0.001 0.05 0.003 10 [18]
received:   session status 20200101000033 n n n 27 0 tmr
queueing   (Q# 1): set time 20240203171306 [19]
received:   comms status 20200101000033 0 1 1224 0 26696 0 1 tmr
received:   motor status 20200101000036 azimuth n 20200101000036 0 48000 180.0 n n 0.1 2752 tmr
queueing   (Q# 1): configure motor 20240203171309 azimuth 180.0 0 360 0.0 -1 0.001 0.05 0.003 10 [20]
received:   motor status 20200101000036 altitude n 20200101000036 000.0nn0.1 3680 tmr
queueing   (Q# 2): configure motor 20240203171309 altitude 0.0 0 90 0.0 -1 0.001 0.05 0.003 10 [21]
received:   motor status 20200101000046 azimuth n 20200101000046 0 48000 180.0 n n 0.1 2176 tmr
queueing   (Q# 1): configure motor 20240203171319 azimuth 180.0 0 360 0.0 -1 0.001 0.05 0.003 10 [22]
received:   motor status 20200101000046 altitude n 20200101000046 000.0nn0.1 2944 tmr
queueing   (Q# 2): configure motor 20240203171319 altitude 0.0 0 90 0.0 -1 0.001 0.05 0.003 10 [23]
received:   session status 20200101000053 n n n 47 0 tmr
queueing   (Q# 1): set time 20240203171326 [24]
queueing   (Q# 2): # heartbeat [25]
received:   comms status 20200101000053 0 1 1678 0 46699 0 1 tmr
received:   motor status 20200101000056 azimuth n 20200101000056 0 48000 180.0 n n 0.1 2560 tmr
queueing   (Q# 1): configure motor 20240203171329 azimuth 180.0 0 360 0.0 -1 0.001 0.05 0.003 10 [26]
received:   motor status 20200101000056 altitude n 20200101000056 000.0nn0.1 2528 tmr
queueing   (Q# 2): configure motor 20240203171329 altitude 0.0 0 90 0.0 -1 0.001 0.05 0.003 10 [27]
```

Short-bus, 2024-02-19:
```
received:   motor status 20200101000016 altitude n 20200101000016 000.0nn0.1 3024 tmr
queueing   (Q# 2): configure motor 20240203171249 altitude 0.0 0 90 0.0 -1 0.001 0.05 0.003 10 [15]
```
The above exchange shows that the RPi is receiving and understanding the microcontroller. The motorcontroller is sending motor status, the RPi understands this is an unconfigured motor so responds immediately with a configuration message. However all the followon status messages from the microcontroller continue to show an unconfigured motor, this suggests that the microcontroller is not receiving or processing the messages from the RPi properly.

The motor status messages include the 'tmr' status code, this indicates WHY the status message was sent. In the log file these are ALL 'tmr' which means the message is just a timed message. If the microcontroller was processing the configure motor messages correctly it respond immediately with a 'cfg' code instead of 'tmr'. This also suggests that the microcontroller is not actually processing the messages.

```
received:   session status 20200101000053 n n n 47 0 tmr
queueing   (Q# 1): set time 20240203171326 [24]
```
The above exchange shows a session status message from the microcontroller, it includes a timestamp - the timestamp is the default 2020.Jan.02 00:00:00 clock. The RPi responds with a 'set time' message to set the clock to the current time. However all the later messages from the microcontroller continue to show the unsynchronised clock. This also suggests that the microcontroller is not receiving or processing the messages.

If the microcontroller was completely crashing we would not receive any further messages.
If the microcontroller was failing and restarting we would see repeated blocks of messages identifying a restart.
Neither is occurring, so the problem is likely to be a non-fatal fault in the microcontroller processing. The most likely reasons being a break in the TX->RX line from the RPi to the microcontroller, or a function call failing on the microcontroller.

To see the precise detail the microcontroller was connected via a USB cable to the RPi and the serial shell output viewed through Thonny. It then was apparent that the microcontroller was running the wrong version of CircuitPython.

The code currently only works on CircuitPython7, the microcontroller was running CircuitPython8 which has syntax changes in the UART module. Downgrading the microcontroller to CircuitPython7.2 should solve the problem.

When the microcontroller first starts communicating it should pass information about the environment including some CircuitPython version information. This will be visible in the RPi log file, you can also trigger this to be resent by pressing the 'reset' button on the microcontroller to trigger a restart.

Later versions of the software compare the reported version number against a list of supported versions and leave a warning in the log file too.

Short-bus, 2024-02-25:
The 2024-01-issues branch includes an updated version of circuitpython/code.py which now also runs on CircuitPython8.

Short-bus, 2024-02-27:
Done.

Closed 2024-02-27.

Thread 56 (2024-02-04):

Initial menu does not recognize the 'x' key

tproffen, 2024-02-04:
It looks like when starting pilomar the very first menu does not recognize the 'x' key and says 'try again'.   Here is the terminal dump

`pi@pilomar:~/pilomar/src $ ./pilomar

SoftwareStartDatetime: 2024-02-04 20:09:45.032943+00:00 UTC
Using realtime clock.
Project root /home/pi/pilomar
Current time is: 2024-02-04 20:09:45.033469+00:00  UTC, offset is None seconds.
pilomar.py 2024-01-30 19:18:18.970106
Main log to /home/pi/pilomar/log/pilomar_20240204200945.log
Camera log to /home/pi/pilomar/log/pilomar_camera_20240204200945.log
Removing out of date log files to preserve disc space...
find /home/pi/pilomar/log -type f -name 'pilomar_*.log' -mtime +2 -delete
Done.
2024-02-04 20:09:45 Loading parameters from file: /home/pi/pilomar/data/pilomar_params.json
Current UTC time is: 2024-02-04 20:09:45.283973+00:00
Local time is: 2024-02-04 15:09:45.283973-05:00
Python3 is UTF-8 compliant, make sure that the terminal is in UTF-8 mode too.
2024-02-04 20:09:45 Initial: Using SD card for images. /
Motors enabled
DetectCamera: raspistill -o /home/pi/pilomar/temp/testraspistill.jpg
WARNING: reported in LogFile: 2024-02-04 20:09:45 DetectCamera: Camera not found.
DetectCamera: False
Camera disabled
2024-02-04 20:09:45 The program will generate simulated images instead.
2024-02-04 20:09:48 azimuth motor restored to last known position 48000 (  180.000° )
2024-02-04 20:09:48 altitude motor restored to last known position 0 (  000.000° )
2024-02-04 20:09:48 Home location Latitude 36.017935 N, Longitude 84.215594 W
2024-02-04 20:09:48 Hipparcos data cache exists, using that.

 Select target
 1 Resume last observation      2 Repeat earlier observations
 3 Solar system object          4 Hipparcos star catalog
 5 Messier catalog              6 New General Catalog (NGC)
 7 Comet                        8 Meteor shower       
 9 Space stations/satellites   10 RA-DEC co-ordinates 
11 Fixed ALT-AZ point  
 x Exit                         ? Refresh            
Menu option : x
? Try again.

 Select target
 1 Resume last observation      2 Repeat earlier observations
 3 Solar system object          4 Hipparcos star catalog
 5 Messier catalog              6 New General Catalog (NGC)
 7 Comet                        8 Meteor shower       
 9 Space stations/satellites   10 RA-DEC co-ordinates 
11 Fixed ALT-AZ point  
 x Exit                         ? Refresh            
Menu option : `

Short-bus, 2024-02-05:
Well spotted, I'll check that out.
As a workaround you can just select '_1 Resume last observation_' to get out of the menu and keep the current selection.
When the program first starts up you have to select a target in order to proceed, but after that it should allow you to back out of target selection and keep the current choice.

Short-bus, 2024-02-05:
Testing solution which reloads the 'last target' automatically if you 'x' out of the target selection menu.
Will be part of the 2024-01-issues branch when ready.

Short-bus, 2024-02-27:
Done.

Closed 2024-02-27.

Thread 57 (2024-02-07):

Simplify microstepping configuration for motors

Short-bus, 2024-02-07:
The original code for handling the stepper motors has support for microstepping, but it is quite old code.
The configuration to support microstepping is hardcoded, and split across src/pilomar.py and circuitpython/code.py.
Any changes have to be made in both programs.
With experience it can be simplified.
There are some builds underway which want to use microstepping so now is a good time to simplify the code.

1. Consolidate all the microstepping related parameters into the parameter file. All programs then take their rules from there.
2. Simplify the code for handling microstepping, the original version has more features than needed but is difficult to test.
3. Make it easier for people to use alternative steppermotor driver boards. The current code expects DRV8825s but some people want to use alternatives.

Short-bus, 2024-02-08:
New solution in the 2024-01-issues branch.

You can now change the stepper motor microstepping setting directly in the parameter file.
AzimuthMicrosteppingRatio and AltitudeMicrosteppingRatio

By default these are '1' meaning FULL STEPS.

You can use 2,4,8,16 or 32 to increase microstepping.

Be sure to restart both the RPi software AND the microcontroller to force the new parameter values to be taken into use.

Short-bus, 2024-02-27:
Done.

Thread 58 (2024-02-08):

Can pilomar run on RPi4B with Bookworm o/s?

Short-bus, 2024-02-08:
Pilomar currently (Jan.2024) runs on Buster O/S 32bit.
The Bullseye release caused too many dependencies to break, so is not used.
Tests show that pi-lomar can be run on RPi5 with Bookworm 64bit.
Can the same be done on an RPi4?
I think that libcamera will be an issue, but hopefully it's relatively straightforward to upgrade to that because the libcamera-jpeg command seems to be backwards compatible with the older raspistill command.

Short-bus, 2024-02-10:
Converted the hardcoded raspistill commands into templates.
These are held in the parameter file.
When the file is initialised the templates are populated with either raspistill or libcamera-still command templates.
The decision is made currently based upon the operating system.
The astrocamera() class uses the templates and populates runtime values as needed.
On Bookworm O/S the separate pidng extract of the raw bayer data is nolonger needed, it's available now as a command line option on libcamera-still.

This is probably the main barrier to running pi-lomar on Bookworm 64bit on the RPi4B, initial tests suggest this gets everything working OK.

This does NOT clear the software to run on a RPi5 yet because that has additional GPIO changes to handle.

The initial build script is much simpler too.

Short-bus, 2024-02-25:
Initial support for Bookworm 64bit on RPi4B has been running now for a couple of weeks on a test build. Have added features into the 2024-01-Issues branch ready for merging back to the main branch.

Short-bus, 2024-02-27:
Done.

Closed 2024-02-27.

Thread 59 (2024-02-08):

ProjectRoot not fully respected

Marcus8675, 2024-02-08:
Noticed at least 1 area in pilomar.py where the new ProjectRoot is not utilized.

FolderList["dataroot"] = "/home/pi/pilomar/data/" # Create default DATA pointer.
FolderList["log"] = "/home/pi/pilomar/log/" # Create default LOG pointer.

Short-bus, 2024-02-09:
Thanks Marcus, This should be fixed in the 2024-01-issues branch.
If it's critical for you, just alter your copy for now.

```
FolderList={} # Dummy entry until FolderList is fully defined. astrocamera doesn't initialize otherwise.
FolderList["dataroot"] = ProjectRoot + "/data/" # Create default DATA pointer.
FolderList["log"] = ProjectRoot + "/log/" # Create default LOG pointer.
```

You can copy the latest code from [2024-01-issues](https://github.com/Short-bus/pilomar/tree/2024-01-issues) too of course - but you'll need to pull ALL the new codes from /src/*.py and also  update /circuitpython/code.py onto the microcontroller.

Thanks for the heads up about it.

Marcus8675, 2024-02-18:
I think I found another hidden spot.  line 1240 in pilomar.py

USBDiscMonitor = discmonitor(name='usb',devname=usbdev,path='/media/pi',disctype='usb',logger=MainLog.Log) # Create USB memory card monitor (if it exists).

If not installed in "/pi" folder then the USB mount will fail with '/media/pi' path

Short-bus, 2024-02-21:
Added 'path' parameters to the parameter file to allow for different mount paths.
Parameters.SDPath = '/' for monitoring the root SD card storage.
Parameters.USBPath = '/media/pi' for monitoring USB connected storage.
If you use different mount points now you can change the above parameters in the parameter file to retain your chosen paths across future software versions.

Have also made a note that the logic for finding the USB storage can be simplified in future. If the RPi starts up the desktop when it boots then the mounting is done automatically and more reliably. The current logic tries to find and mount USB storage even if there is no desktop running, but it is over-complex compared to having the desktop launched.

Short-bus, 2024-02-27:
Keeping this one open after the latest updates because I want to review the logic and simplify it further. But there is now a workaround in place for USB storage which is mounted under alternative paths.

Marcus8675, 2024-02-28:
May want to check your build scripts also for the new path parameters.  I think I saw some fixed paths in there.

Short-bus, 2024-07-10:
2024-04 Development branch now merged.
Closes this issue.

Closed 2024-07-10.

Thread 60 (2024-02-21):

Simplify USB storage handling

Short-bus, 2024-02-21:
The 'discmonitor' class in src/pilomardisc.py tries to find and mount USB storage if the RPi is running without the desktop being launched.
If the desktop is automatically launched in the background when the RPi boots (raspi-config option) then the USB storage mounts automatically and more reliably.
The code in discmonitor can therefore be simplified and more reliable if the decision is made to always have the desktop launched on startup if you want to use attached storage.

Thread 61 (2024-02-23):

Scheduled Observations

Marcus8675, 2024-02-23:
Enhancement feature.  Options to schedule observations.  Foe example, ISS will be over my area from 8:42-8:53pm tonight.  I want to set up the system, tune and home all the motors, and schedule it to automagicly start the observation at the correct time.  Bonus if I can plan a full night of observations on multiple targets at various times.  would be a nice scheduling feature.  I could just follow up at the end of the evening with bias, dark and dark flats.

Short-bus, 2024-02-23:
I imagine it can be done. It would require a few new features I guess.

- A way to maintain an observation queue. (The solution used for recording 'previous targets' may be the basis?)
- A parent loop for the main ObservationRun routine to loop through the queue and switch target as needed. (Probably OK, I tried a 'survey' function which does something similar in an experimental program).
- A cut-off clock for ObservationRun to quit each observation at the right time. (Could be an attribute of the target when it's selected)

When it comes to imaging the ISS are you thinking to keep the ISS centre of the image, or park the telescope at just the right spot to catch it passing through the field of view?

Parking requires a simple ALT-AZ target to be used - you 'just' have to calculate the optimum ALT-AZ locations. I think the skyfield package can help with that calculation.

Tracking is more tricky: The ISS motion is at the upper limit of the telescope's speed so that may have an impact somewhere. Also with short lived time critical targets like that you need to consider the 'cycle time' between successive images. _This is similar to another builder's question about imaging eclipses._ It may be necessary to strip out all unnecessary tasks from the observation for the duration of the pass so you get the maximum number of images caught. I suspect you'd need some sort of 'loiter' function so that the telescope can pre-position itself ready for the ISS to pass into the field of view. So something special in the way the trajectory is calculated?

Marcus8675, 2024-02-23:
The ISS was just an example (and a bad one) but I guess you could park it and image it like meteor detection.

I do like how you are already envisioning the implementation structure.  Let me try to explain the ideal end state that I had in mind.  Note that I absolutely do not expect this to be achieved quickly or at all but you know...to reach the clouds you have to aim for the stars.  :)

I was envisioning a final state where the PiLomar is outside for extended periods, if not in a permanent installation.  Remotely, I can schedule observations.  Love to have a calendar of upcoming solar events (comet xyz on Tuesday, Planet pdq rises on Thursday, etc..) and be able to plan my daily/weekly observations from the warm comfort of 'remote location'.  Starting to think about how to automate lens caps for end of session and dark files.  But this step is really about the first baby step to the end state.  Lets say on Friday I want to image Jupiter for the first 2 hrs, and then once that is past its prime viewing area, I would transition to Orion Nebula for an hr or so.  I can see a world where I spend my Saturday stacking and processing images from the prior week discounting the cloud covered days.

Short-bus, 2024-07-07:
This isn't implemented yet, but the next release has some preparation changes.
I've made a more general purpose solution to the 'target history' handling.
The format is more flexible so can also be used to handle lists of observations for other purposes.

2 additional uses come to mind at the moment.
1) The 'schedule' that you have raised here.
* I still need to think about how to achieve a simple and reliable solution to this one. But I really like the idea.
2) A list of 'suggested targets' that could be calculated.
* The software could run through the planet, comet, satellite, messier and NGC catalogs and list the brightest or largest targets that will be visible for your location. I wouldn't make it run through the Hipparcos catalog though... 100,000 stars could take a while :)
* I still need to consider an efficient way to filter these lists.

In the next release it's only used for remembering recent observations.

Closed 2025-04-20.

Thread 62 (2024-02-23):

Observing an eclipse with pilomar

Short-bus, 2024-02-23:
wyoming4wheeler on Instructables asked :

`Does anyone have suggestions on how to setup the software to capture the up coming eclipse. I have scheduled a campground in the middle of Missouri to be able to setup and capture the eclipse and hopefully the devil comet all at the same time. I am concerned about the length of time of captures considering I will only have 4 minutes of the actual eclipse - but I want to make sure I am capable to capture the comet as well. Just started trying different captures. Also, do I need to use the daystar solar filter that I bought to use with the lens. Not sure whether the camera sensor will be fried looking directly at the sun.`

Short-bus, 2024-02-23:
The eclipse... there's an exciting challenge.

Some immediate thoughts...

Disable a few features. You don't want it to start doing admin tasks mid observation.

Set UseTracking to false in the parameter file.
Set GeneratePreview to false in the parameter file.
Set ScanForMeteors to false in the parameter file.
If you're set up in plenty of time you can manually 'tune' the position via the motor menu, or from within the observation by pressing the 'm' key. You could do this by examining the .jpg files as they arrive in the /light folder. Print out a copy of a 'preview' image from the /preview folder in advance and us that as a reference for the adjustment values. It should keep the sun in frame for you for quite some time if setup and tuned manually.

The 'cycle time' between exposures will be quite short so you should be able to capture plenty of images. There's a quirk of 'raspistill' that the cycle time can be double the exposure time - which is noticeable for 20 second exposures, but negligible for really fast ones.

I wonder if video would be better than separate images, that's not in the current software. But you may be able to adjust the program to achieve it somehow, especially if the tracking and preview features are off.

Obviously make sure you've plenty of storage space available. You can insert a USB 3.1 memory stick into one of the blue USB 3 ports on the RPi. Format it with the label 'USBMEMORY' and I think it will auto-mount and get used automatically if you have the RPi set to boot to the desktop in raspi-config. The UseUSBStorage parameter defaults to 'true' so it should switch to using it if it's detected.

I'd expect you'd need a solar filter to protect the sensor, but haven't tried it. And I'd close the aperture down a lot too.

I'll think further on it, hopefully others have experience already of photographing an eclipse and let us know!

Short-bus, 2024-02-23:
To have TWO objects in the image at the same time I suppose you would want a RADEC target which is between the two actual objects.
You could build a python query using skyfield to calculate the RADEC coordinates of the sun and of the comet at the time of the eclipse and calculate the midpoint of those two locations. Then in pilomar create your own RADEC target with that averaged position. You can do this in advance, so it's available to you on the day in the 'repeat earlier observations' list.

Short-bus, 2024-11-22:
No further action on this one so closing it.

Closed 2024-11-22.

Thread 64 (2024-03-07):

piDNG.convert in new bookworm build fails

Marcus8675, 2024-03-07:
preview and auto seem to work but when first light image is take the code exits due to failure to DNG convert.  output is listed below:

In DEBUG MODE. The dashboard display is suppressed so that any errors are more clear.
In DEBUG MODE. Press 'x' to quit, 'd' toggle debug, 'm' submenu, 'r' refresh.
2024-03-06 12:46:11 ObservationRun: (DebugMode) Starting main loop...
12:46:35 ReadyToObserve changed from False to True
12:46:35 Begin tracking image capture.
12:46:49 Begin image capture (1) 1.0s.
2024-03-06 12:47:03 logfile.RecordTraceback(): ErrorMessage 'NoneType' object has no attribute 'convert'
2024-03-06 12:47:03 logfile.RecordTraceback(): Traceback (most recent call last):
2024-03-06 12:47:03 logfile.RecordTraceback():   File "/home/pi/pilomar/src/pilomar.py", line 2417, in CaptureSetFull
2024-03-06 12:47:03 logfile.RecordTraceback():     PiDNG.convert(outputfile) # Convert the saved .jpg file into the raw .dng format.
2024-03-06 12:47:03 logfile.RecordTraceback():     ^^^^^^^^^^^^^
2024-03-06 12:47:03 logfile.RecordTraceback(): AttributeError: 'NoneType' object has no attribute 'convert'
2024-03-06 12:47:03 logfile.RecordTraceback():
** ERROR ** reported in LogFile: 2024-03-06 12:47:03 logfile.RaiseException(): Comment: astrocamera.CaptureSetFull(): PiDNG.convert failed.
** ERROR ** reported in LogFile: 2024-03-06 12:47:03 CameraHandler: CameraInUse.TakePhoto failed.
** ERROR ** reported in LogFile: 2024-03-06 12:47:03 CameraHandler: CameraInUse.TakePhoto raised:Program exception raised
** ERROR ** reported in LogFile: 2024-03-06 12:47:03 logfile.ReportException(): Error Program exception raised
2024-03-06 12:47:03 logfile.RecordTraceback(): ErrorMessage Program exception raised
2024-03-06 12:47:03 logfile.RecordTraceback(): Traceback (most recent call last):
2024-03-06 12:47:03 logfile.RecordTraceback():   File "/home/pi/pilomar/src/pilomar.py", line 2417, in CaptureSetFull
2024-03-06 12:47:03 logfile.RecordTraceback():     PiDNG.convert(outputfile) # Convert the saved .jpg file into the raw .dng format.
2024-03-06 12:47:03 logfile.RecordTraceback():     ^^^^^^^^^^^^^
2024-03-06 12:47:03 logfile.RecordTraceback(): AttributeError: 'NoneType' object has no attribute 'convert'
2024-03-06 12:47:03 logfile.RecordTraceback():
2024-03-06 12:47:03 logfile.RecordTraceback(): The above exception was the direct cause of the following exception:
2024-03-06 12:47:03 logfile.RecordTraceback():
2024-03-06 12:47:03 logfile.RecordTraceback(): Traceback (most recent call last):
2024-03-06 12:47:03 logfile.RecordTraceback():   File "/home/pi/pilomar/src/pilomar.py", line 8157, in CameraHandler
2024-03-06 12:47:03 logfile.RecordTraceback():     result = CameraInUse.TakePhoto(batch_size,terminal=False)
2024-03-06 12:47:03 logfile.RecordTraceback():              ^^^^^^^^^^^^^^^^^^^^^^^^^^^^^^^^^^^^^^^^^^^^^^^^
2024-03-06 12:47:03 logfile.RecordTraceback():   File "/home/pi/pilomar/src/pilomar.py", line 2524, in TakePhoto
2024-03-06 12:47:03 logfile.RecordTraceback():     result = self.CaptureSet(file_root=FileRoot,batch_size=batch_size,camera_command=CameraCommand,terminal=terminal,cleanup=False)
2024-03-06 12:47:03 logfile.RecordTraceback():              ^^^^^^^^^^^^^^^^^^^^^^^^^^^^^^^^^^^^^^^^^^^^^^^^^^^^^^^^^^^^^^^^^^^^^^^^^^^^^^^^^^^^^^^^^^^^^^^^^^^^^^^^^^^^^^^^^^^^^^
2024-03-06 12:47:03 logfile.RecordTraceback():   File "/home/pi/pilomar/src/pilomar.py", line 2346, in CaptureSet
2024-03-06 12:47:03 logfile.RecordTraceback():     result = self.CaptureSetFull(file_root,batch_size,camera_command,tempfile=tempfile,terminal=terminal,cleanup=cleanup,astrotime=astrotime)
2024-03-06 12:47:03 logfile.RecordTraceback():              ^^^^^^^^^^^^^^^^^^^^^^^^^^^^^^^^^^^^^^^^^^^^^^^^^^^^^^^^^^^^^^^^^^^^^^^^^^^^^^^^^^^^^^^^^^^^^^^^^^^^^^^^^^^^^^^^^^^^^^^^^^^^^^^^
2024-03-06 12:47:03 logfile.RecordTraceback():   File "/home/pi/pilomar/src/pilomar.py", line 2419, in CaptureSetFull
2024-03-06 12:47:03 logfile.RecordTraceback():     CamLog.RaiseException(e,comment='astrocamera.CaptureSetFull(): PiDNG.convert failed.')
2024-03-06 12:47:03 logfile.RecordTraceback():   File "/home/pi/pilomar/src/pilomarlogfile.py", line 173, in RaiseException
2024-03-06 12:47:03 logfile.RecordTraceback():     raise Exception('Program exception raised') from e # Terminate through regular exception stack.
2024-03-06 12:47:03 logfile.RecordTraceback():     ^^^^^^^^^^^^^^^^^^^^^^^^^^^^^^^^^^^^^^^^^^^^^^^^^^
2024-03-06 12:47:03 logfile.RecordTraceback(): Exception: Program exception raised
2024-03-06 12:47:03 logfile.RecordTraceback():
** ERROR ** reported in LogFile: 2024-03-06 12:47:03 logfile.ReportException(): Comment: CameraHandler: Call to TakePhoto()
** ERROR ** reported in LogFile: 2024-03-06 12:47:03 CameraHandler: Something went wrong with image capture. Aborting.
2024-03-06 12:47:03 CameraHandler: Finished.
** ERROR ** reported in LogFile: 2024-03-06 12:47:03 ObservationRun: CameraThread (Camera handler) is not running!

Stopping CameraHandler...
Waiting for CameraHandler to confirm it has completed (telescope may continue to move until this is finished) ...

Short-bus, 2024-03-07:
Hmm... looks like it's trying to extract the .DNG data from a raspistill image but doesn't have the PiDNG library loaded. I can't recreate the error immediately in Buster or Bookworm...

... digging ...

OK, I compared my running version with the GitHub version, looks like I messed up the merge. I'll repost the src/pilomar.py code again...

Short-bus, 2024-03-07:
Try downloading src/pilomar.py and giving it another go.

Marcus8675, 2024-03-08:
That solved it!  Thanks for the update.  Can you do anything about these clouds? :(

Short-bus, 2024-03-08:
Great. Thanks for raising it, I have 4 instances running in different configurations - I missed that 'raspistill' check from the mastercopy, but my local instance was OK. I'll close this one now.

> Can you do anything about these clouds? :(

I can only sympathise on that one. There was a good aurora display a few days ago here, 100% cloud cover coincided precisely with the show. We've chosen an infuriating sport I think :)

Closed 2024-03-08.

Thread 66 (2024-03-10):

On chip cleanup not functional in new Bookworm build

Marcus8675, 2024-03-10:
I was unable to disable the on chip cleanup using the new build on a Bookworm system.  Changing the setting to false in the pilomar.json file had no effect.  Upon boot on chip cleanup was listed as ENABLED.  Using the camera menu to disable this feature also seems to have no effect.  When camera information is displayed from this menu if always shows ENABLED.  The main capture window also shows ENABLED.

Short-bus, 2024-03-10:
Hi. Well spotted, I'll need to clean up the UI a bit for that. Good to have a second pair of eyes running over it all.

Under Bookworm the camera is run by libcamera and that now has the 'denoise' option when you call it.
So the libcamera command templates (in the parameter file) have the '--denoise off ' option set in each case.
As a result the earlier onchip cleanup solution is only used with Buster builds.
So the onchip cleanup references are misleading under Bookworm because it's handled differently. I'll need to do some tidying up, I'd not noticed that inconsistency earlier, but it makes sense to hide that misleading info on a Bookworm install.

With this latest version I've moved more camera options into the command templates instead of having them hardcoded into the program. So hopefully overall it's easier to play with different camera settings as needed.

Short-bus, 2024-03-11:
Testing modified logic.

### In Buster:
The original DisableCleanup parameter and UI references work as before.

### In Bookworm:
The DisableCleanup parameter will be removed.
The UI references now check the CameraLightCommand parameter to see if the '--denoise off' parameter is set.
If you try to enable/disable cleanup via the menu options it will recommend that you edit the command templates in the parameter file.
To enable on-chip cleanup, remove the '--denoise off' item from the command templates.
To disable on-chip cleanup, add the '--denoise off' item to the command templates.
The default templates have '--denoise off' in place. So you have to choose to turn on-chip cleanup back on.

Short-bus, 2024-07-10:
2024-04 Development branch now merged.
Closes this issue.

Closed 2024-07-10.

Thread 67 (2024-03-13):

FindUSB fails if new USB memory stick has no label.

Short-bus, 2024-03-13:
Problem spotted by -PHU-

```
When I bought a new 32 GB stick recently, I ran into a certain weakness in pilomardisk.py.
A USB stick normally has four identifiers: amount of storage, file system, (own) serial ID and a label. This information is identified in pilomardisk.py by the process:  def FindUSB.
When a fresh USB device is introduced, this device carries no label. The program pilomardisk.py then crashes on line 164, as the fourth item is empty.
In Linux and Windows normally the label is shown, but in case the label is absent, the serial number is shown. I think pilomardisk.py needs such a provision too.
```

Review the way USB memory is recognised and used. For example, is it is simpler to rely upon the RPi always booting to the desktop in order to find and mount the memory?

Short-bus, 2024-04-26:
Latest copy in development will default back to SD card storage and issues a warning with common causes if USB storage search fails unexpectedly.

Short-bus, 2024-07-10:
2024-04 Development branch now merged.
Closes this issue.

Closed 2024-07-10.

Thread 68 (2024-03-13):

Microcontroller MoveMotor() more efficient mode and direction signals.

Short-bus, 2024-03-13:
circuitpython/code.py

The original code repeats setting the 'mode' and 'direction' signals for each individual step. This is a throwback to earlier code which supported synchronised movement of motors. In the current program only 1 motor moves at a time, so the mode and direction signals only need setting at the start of the move. This reduces a little processing overhead from each move pulse cycle.

The 'mode' and 'direction' signals could be relocated from MoveFullStep() to the start of MoveMotor(). Estimate 15% cycle time saved for each step.

Short-bus, 2024-04-26:
The MoveFullStep and MoveMotor methods are refactored in the latest development copy.
It takes this issue into account.

Short-bus, 2024-07-09:
'Observation' and 'Slew' moves are now supported with the new code. This means the telescope can perform GOTO and HOME movements more rapidly, but when making observations it can then use finer motor control.

Added function to the menu to select from some recommended move/stepping possibilities. For example when combining microstepping and faster 'slew' movements.
The latest version has multiple parameters available for controlling how movements are made, there is a risk that manually editing the parameter file may leave some parameter options in an incompatible state.
By using the menu options it should always configure a valid combination of parameter settings.

Short-bus, 2024-07-10:
2024-04 Development branch now merged.
Closes this issue.

Closed 2024-07-10.

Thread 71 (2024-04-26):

Running circuitpython/code.py on CircuitPython 9.0

Short-bus, 2024-04-26:
Have tried to install CircuitPython 9.0 on Tiny2040 microcontroller to see if circuitpython/code.py runs OK on the latest image.
Currently the Thonny (and Mu Editor) tools crash out when trying to talk to a CircuitPython 9.0 device.
The microcontroller is flashing the RGB LED RED just after it boots which indicates a problem, but unable to see what the cause is.
Currently recommending stick to CircuitPython 7.2 and 8.2 images.

Short-bus, 2024-09-19:
CircuitPython 9.1 works OK on new Tiny2350 which has more RAM available. It doesn't look like the Tiny2040 can support the current pilomar functions AND Circuitpython 9.x at the same time.
To use CP 9.x it seems that upgrading to a Tiny2350 is the simplest solution.

Closed 2024-09-19.

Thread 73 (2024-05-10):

Save Raspberry Pi Hi Quality Camera images as .FITS format

Short-bus, 2024-05-10:
Several astro packages and utilities work with raw image data stored in .fits format.
raspistill (+pidng), and libcamera (via pidng) can export raw data in .dng format, but not as .fits files.

The picamera2 library allows the raw matrix data to be exported from the camera.
Can that data be saved as a .fits file?

The astropy library includes the pyfits module, this allows numpy arrays (and more) to be written to .fits files.

To maintain compatibility with the current architecture of the pi-lomar project it would be nice to offer a 'command line' way to capture an image and produce the .fits file. Something similar to ...
`libcamera-still --output {&output} --timeout 1 --nopreview --quality 100 --width {&width} --height {&height} --denoise off --analoggain 16.0 --shutter {&shutter}`

I am testing a python script 'pilomarfits.py' for the next release which can be called in a similar way, using similar syntax but which will produce a basic .fits file and an unprocessed .jpg file as output.

`python3 pilomarfits.py --output {&output} --quality 100 --width {&width} --height {&height} --shutter {&shutter} --tuning-file imx477_noir.json`

This accepts the same command line options as the libcamera utilities so that pilomar.py can switch between the two solutions more easily. In the first version this will only implement the minimum command line options needed to produce an unprocessed .fits copy of the bayer data and an unprocessed .jpg file of the image in color. The .jpg files are 'unprocessed' in that they have no automatic exposure or white balance calculation, they are just simple debayered copies of the raw data.

If successful, pi-lomar can then use whichever driver you need.

- raspistill on old Buster builds (eg on RPi 3). Producing .dng and .jpg images.
- libcamera on Bookworm builds (eg on RPi4 & 5). Producing .dng and .jpg images.
- pilomarfits.py on Bookworm builds (eg on RPi4 & 5). Producing .fits and .jpg images.

This solution will not allow .fits exports on earlier O/S builds, it will need to be Bookworm or above.
pilomarfits.py uses OpenCV to perform colour image functions and saving, so could be expanded further to save in some other formats if needed in the future too.

Short-bus, 2024-07-09:
Added option to the camera menu to select which image types should be saved.
That makes sure you can only select valid combinations of image types to save.
It then selects the appropriate driver and commands to support the chosen driver and image types.
This is safer than manually editing the parameter file, it reduces the risks of incompatible values being selected.

Short-bus, 2024-07-10:
2024-04 Development branch now merged.
First version of a solution for FITS files now available.

Closed 2024-07-10.

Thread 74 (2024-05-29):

NGC catalog build fails if user is not 'pi'

Short-bus, 2024-05-29:
Raised by unhuzpt

Is this something you already know about?
I am running in bookworm with full install :)

`Camera enabled
2024-05-28 10:25:28 No recovery log file found for azimuth motor. Assuming  180.000Â°
2024-05-28 10:25:28 No recovery log file found for altitude motor. Assuming  000.000Â°
2024-05-28 10:25:28 Home location Latitude 49.781880 N, Longitude 6.225176 E
2024-05-28 10:25:28 Hipparcos data cache exists, using that.
[#################################] 100% de421.bsp
2024-05-28 10:25:35 Loading Messier catalog from /home/unhuzpt/pilomar/data/messierobjects.json ...
[#################################] 100% constellationship.fab
2024-05-28 10:25:36 Loading constellation patterns...
2024-05-28 10:25:36 Loading New General Catalog (NGC) entries from /home/unhuzpt/pilomar/data/ngc.json ...
2024-05-28 10:25:36 No NGC data cache, creating one now.
Exception in thread Thread-1 (StartMctlComms):
Traceback (most recent call last):
  File "/usr/lib/python3.11/threading.py", line 1038, in _bootstrap_inner
    self.run()
  File "/usr/lib/python3.11/threading.py", line 975, in run
    self._target(*self._args, **self._kwargs)
  File "/home/unhuzpt/pilomar/src/pilomar.py", line 3472, in StartMctlComms
    Mctl.CommsLoop(UartControlQueue)
  File "/home/unhuzpt/pilomar/src/pilomar.py", line 3404, in CommsLoop
    self.ReadPoll() # Read anything waiting in the input buffer.
    ^^^^^^^^^^^^^^^
  File "/home/unhuzpt/pilomar/src/pilomar.py", line 3226, in ReadPoll
    while self.uart.in_waiting: # Something in the read queue.
          ^^^^^^^^^^^^^^^^^^^^
  File "/usr/lib/python3/dist-packages/serial/serialposix.py", line 549, in in_waiting
    s = fcntl.ioctl(self.fd, TIOCINQ, TIOCM_zero_str)
        ^^^^^^^^^^^^^^^^^^^^^^^^^^^^^^^^^^^^^^^^^^^^^
OSError: [Errno 5] Input/output error
2024-05-28 10:26:12 Loading meteor shower list from /home/unhuzpt/pilomar/data/meteors.json ...
2024-05-28 10:26:12 Loading comet list from https://www.minorplanetcenter.net/iau/MPCORB/CometEls.txt ...
[#################################] 100% CometEls.txt
2024-05-28 10:26:14 Loading CelesTrak station data from https://celestrak.org/NORAD/elements/gp.php?GROUP=stations&FORMAT=tle
You must select a target to start the program.

 Select target
 1 Resume last observation      2 Repeat earlier observations
 3 Solar system object          4 Hipparcos star catalog
 5 Messier catalog              6 New General Catalog (NGC)
 7 Comet                        8 Meteor shower       
 9 Space stations/satellites   10 RA-DEC co-ordinates 
11 Fixed ALT-AZ point  
 x Exit                         ? Refresh            
Menu option :

`

_Originally posted by @unhuzpt in https://github.com/Short-bus/pilomar/discussions/72#discussioncomment-9579461_

Short-bus, 2024-05-29:
Additional info from unhuzpt:

So......
Yeah, the "issue" was that your script assumes the user is 'pi' and that was not my case :)
So tired lately that i forgot this when i build the 1st time and noticed it....
Now it installed all fine and is working as expected :)

Allow me to suggest maybe to adapt the script to something like:

#Get current user
username=$(whoami)

#use current user
export pilomarhome="/home/${username}/pilomar"

Or maybe even ask if one wants to use the current user or another?

Short-bus, 2024-05-29:
The program should adapt to different users, so there's a bug somewhere.
Needs investigating.

unhuzpt, 2024-05-30:
I think for my case there were 2 points that made it work:

- i forgot to disable the console to serial port
- i had to manually edit the file scripts/buildpilomar_bookworm64

In the installer script the first lines were with user pi so would not create the correct folders and place files on the right place:

export pilomarhome='/home/pi/pilomar'
echo home directory is: $pilomarhome
export pilomarlog='/home/pi/pilomar/log/buildpilomar_bookworm64.log'
echo build logfile is: $pilomarlog

Now as i am under a lot of fatigue this week i really do not remember the sequence of events.
I think after the errors on the installation, i ended up on changing the  file "file scripts/buildpilomar_bookworm64" replacing pi by unhuzpt and then it installed correctly. And maybe only afterwards i disabled the console to serial output.
But i may be wrong.

[pilomar_20240528102522.log](https://github.com/Short-bus/pilomar/files/15493836/pilomar_20240528102522.log)
[pilomar_20240528093337.log](https://github.com/Short-bus/pilomar/files/15493838/pilomar_20240528093337.log)
[pilomar_20240528093140.log](https://github.com/Short-bus/pilomar/files/15493845/pilomar_20240528093140.log)
[pilomar_20240529161918.log](https://github.com/Short-bus/pilomar/files/15493864/pilomar_20240529161918.log)
[pilomar_20240529161918.log](https://github.com/Short-bus/pilomar/files/15493869/pilomar_20240529161918.log)

unhuzpt, 2024-05-30:
I found a cell picture i took to look into the issue, this was on the 27th and the log dir only has 28 and 29 so here it is where is clear things went right after i edited the installer script.
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

Short-bus, 2024-05-30:
Great, thanks, I'll fix those for the next release.
Plus: If I can trap the UART error it can make a suggestion to check the serial console too.

unhuzpt, 2024-05-30:
Something like:

# Create communication with microcontroller over uart0 serial port.
    mctl = microcontroller(port='/dev/serial0',resetpin=Parameters.MctlResetPin,boardtype=Parameters.BoardType)
except PermissionError as e:
    print(f"Error: {e}. Please check the permissions of /dev/serial0.")
    log.error("Failed to open serial port due to permission error")

Maybe can improve this if i take some time to look at the code with more time :)

Short-bus, 2024-07-07:
I've added the specific PermissionError exception check to the code, with an explanation about the SERIAL port configuration.

Short-bus, 2024-07-10:
2024-04 Development branch now merged.
Closes this issue.

Closed 2024-07-10.

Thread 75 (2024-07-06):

Closed door possibility?

kf6spf, 2024-07-06:
Hi ...

A fascinating project that does just about what I was looking for. Great work.

My big question is how the (fixed) dome handles weather? I'm here in "sunny" California, but even we get weather sometimes. How would this dome protect the camera and electronics from wind and water damage?

I have an AllSky camera set up running now, and have had to disable daytime images because the Pi4b running it gets way too hot. I'll have to redesign my pier mount to add fans and heat dissipation somehow. So the second question is how well does this handle excess heat and how would/should one dissipate it?

Michael

Short-bus, 2024-07-07:
Thanks Michael,

The current design definitely isn’t weatherproof enough. I think at least one other builder is looking at an evolution of the project that would be more sealed.

The most obvious gap being the lack of doors, but there are also other gaps to close off. It could all be done. I’ve not tried that yet. I don’t know if the bearing ring would need protecting too? I’m near the sea, everything corrodes here eventually.

Once the dome is sealed you are right there’s a heat problem. The original design uses passive cooling because we have cold enough nights up here. I’m currently experimenting with a RPi5 and I’m using the combined heatsink and fan on that.
For me the captured heat in the dome is a good microclimate to reduce condensation, but it’s a double edged sword.

For heat protection during the day, maybe the dome could be silvered or insulated?

Another thought, forget sealing the dome entirely and build a larger outer cover more simply? Uglier, but practical.

I’ve seen a revised camera cradle design that seals the camera board and adds a heatsink. The RPi and motorcontroller board could be relocated to a cooled and sealed container, that may be simpler than adding cooling and vents to the dome.

It’s possible to add doors in a few ways I guess. Either to make working sliding doors just like a full scale dome, or maybe have a fixed cover that the dome could rotate up against when not in use? (That would block the view of the sky where the cover is fixed, but would not require any additional electronics or motors.) Making sliding working panel doors would look fantastic, but could be an engineering challenge, probably needing a rethink of the microcontroller and PCB.

The published project doesn’t have weather detection, but it could be added. Humidity, wind and rain detection should be possible, there are plenty of free GPIO ports free on the RPi. I made a utility routine that uses metcheck.com’s json feed to give a ‘forecast’ and plan my observations around that. They provide weather and astro forecast web services for free. I’ve found them remarkably reliable.

Also, choose the materials wisely of course. I use PLA+ which is stable enough for our climate, but in high heat I think you need to use a more temperature stable material.

There are many directions to take the project, currently I’m concentrating on the image handling side. It’s going slowly because we have had unbelievably cloudy nights for about a year, and the summer nights are short and light.

If you re-post the question on the [Instructables project](https://www.instructables.com/Pi-lomar-3D-Printed-Working-Miniature-Observatory-/) page, there may be ideas from others too.

Matt

DragonPrincess78, 2024-07-08:
Hi Michael,
what you are asking is exactly the project we are working on. Electric doors and rain detection.
The door mechanism itself is however not easy to build. Considering the size, you will need guide rails on top and bottom. We've got linear steppers on the bottom, and even with 5mm PETG with 35% infill the shutter doors have too much flex and get stuck. I'm currently abroad for work, but once I'm home again, I'll send you photos.
Rain sensing kind of works... we've got those rain drop sensors, which do sense drops, but it takes a lot to get them to engage properly. The camera itself is rainproved with laser cut eva foam and a housing. The control pi got its own housing in the back, with air intakes rain protected too. The only thing which is still in the open are the steppers.
This should be okay, but you will need to clean the lense after each rain anyway.

Material wise, I suggest using PETG or infused filament, maybe HIPS. PLA+ or ABS do not even work in UK summer from experience.

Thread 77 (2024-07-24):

Comet positions fail in Skyfield timelib.py julian_day() function.

Short-bus, 2024-07-24:
When testing on recent RPi5 build, found that comet positions nolonger calculate.
The positions fail in the skyfield timelib.py julian_day() function with the following error.

```
Traceback (most recent call last):
  File "/home/pi/pilomar/src/pilomar2.py", line 7927, in <module>
    Session.Target = TargetSelection()
                     ^^^^^^^^^^^^^^^^^
  File "/home/pi/pilomar/src/pilomar2.py", line 7893, in TargetSelection
    elif option == "COMET": obstarget = ChooseComet()
                                        ^^^^^^^^^^^^^
  File "/home/pi/pilomar/src/pilomar2.py", line 6801, in ChooseComet
    p = planets['sun'] + mpc.comet_orbit( row, ts, GM_SUN)
                         ^^^^^^^^^^^^^^^^^^^^^^^^^^^^^^^^^
  File "/usr/lib/python3/dist-packages/skyfield/data/mpc.py", line 222, in comet_orbit
    t_perihelion = ts.tt(row.perihelion_year, row.perihelion_month,
                   ^^^^^^^^^^^^^^^^^^^^^^^^^^^^^^^^^^^^^^^^^^^^^^^^
  File "/usr/lib/python3/dist-packages/skyfield/timelib.py", line 299, in tt
    whole, fraction = self._jd(year, month, day, hour, minute, second)
                      ^^^^^^^^^^^^^^^^^^^^^^^^^^^^^^^^^^^^^^^^^^^^^^^^
  File "/usr/lib/python3/dist-packages/skyfield/timelib.py", line 210, in _jd
    whole = julian_day(a(year), a(month), a(day), cutoff) - 0.5
            ^^^^^^^^^^^^^^^^^^^^^^^^^^^^^^^^^^^^^^^^^^^^^
  File "/usr/lib/python3/dist-packages/skyfield/timelib.py", line 955, in julian_day
    year = year + y
           ~~~~~^~~
numpy.core._exceptions._UFuncNoLoopError: ufunc 'add' did not contain a loop with signature matching types (dtype('<U4'), dtype('float64')) -> None
```
The mpc comet file is recent and initially looks healthy, however the code fails at the same point for every comet in the mpc list.

The julian_day() function looks like this...

```
def julian_day(year, month=1, day=1, julian_before=None):
    """Given a calendar date, return a Julian day integer.

    Uses the proleptic Gregorian calendar unless ``julian_before`` is
    set to a specific Julian day, in which case the Julian calendar is
    used for dates older than that.

    """
    # Support months <1 and >12 by overflowing cleanly into adjacent years.
    y, month = divmod(month - 1, 12)
    year = year + y
    month += 1

    # See the Explanatory Supplement to the Astronomical Almanac 15.11.
    janfeb = month <= 2
    g = year + 4716 - janfeb
    f = (month + 9) % 12
    e = 1461 * g // 4 + day - 1402
    J = e + (153 * f + 2) // 5

    mask = 1 if (julian_before is None) else (J >= julian_before)
    J += (38 - (g + 184) // 100 * 3 // 4) * mask
    return J
```

The error message suggests a type mismatch between 'year' and 'y'. Maybe one is a numpy array, and the other isn't?

Short-bus, 2024-07-24:
Refreshing the CometEls.txt file solved the problem.
The value on disc appeared to be incompatible in some way.

Solution: Refresh the comet data file on disc.

1) Purge /home/pi/pilomar/data/CometEls.txt
2) Restart the pilomar program

Closed 2024-07-24.

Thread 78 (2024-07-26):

Typo in src/pilomarfits.py - fails checking for --raw switch.

Short-bus, 2024-07-26:
The following command fails...

```
pi@pilomar3:~/pilomar/src $ python3 pilomarfits.py --output /media/pi/USBMEMORY/campaign_ngc2632_e1.0s/session_20240726170315/light/light_20240726170430_00.jpg --quality 100 --width 4056 --height 3040 --shutter 1000000 --metadata --tuning-file imx477_noir.json --numpyfile --raw
Traceback (most recent call last):
  File "/home/pi/pilomar/src/pilomarfits.py", line 261, in <module>
    temp = Argumentdict['--raw']['all'] # Was an overriding filename specified?
           ^^^^^^^^^^^^
NameError: name 'Argumentdict' is not defined. Did you mean: 'ArgumentDict'?
```

Short-bus, 2024-07-26:
Appears to be a typo in the code. Checking correction.

Short-bus, 2024-07-26:
Closed. After double-checking, the published code does not have the error. It's only in recent development changes.

Closed 2024-07-26.

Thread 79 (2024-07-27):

pilomarfits.py .jpg images don't apply analoggain

Short-bus, 2024-07-27:
src/pilomarfits.py captures the raw bayer data directly from the sensor and saves it in .fits format.
It also 'debayers' the data and saves it as a .jpg file so that you can see what was captured.
The current 'debayer' solution does not apply analoggain to the .jpg data, so the resulting file is very dark.
When using raspistill or libcamera-still the analoggain is usually set to 16.0 which produces brighter images.
pilomarfits.py needs to apply the --analoggain parameter to the debayered image before saving.
In the parameter file the templates can then be edited to add '--analoggain 16.0' to each pilomarfits command.

Closed 2025-04-20.

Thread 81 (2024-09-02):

Support for Pimoroni Tiny2350

Short-bus, 2024-09-02:
Pimoroni Tiny2350 is now available with increased memory and higher performance.
Previous Tiny2040 is maxed out with the current version of code.py and does not seem to have the capacity to run CircuitPython later than 8.2 with the pi-lomar software at the same time.
Retain support for Tiny2040 with existing code.py
Add a separate updated version of code.py to be used on the Tiny2350 and taking advantage of its extra capacity.
Add subdirectories to /circuitpython to hold the Tiny2040 and Tiny2350 versions separately.

Short-bus, 2024-09-03:
Opened branch https://github.com/Short-bus/pilomar/tree/Pimoroni-Tiny2350

Short-bus, 2024-09-05:
circuitpython folder rearranged to hold original Tiny2040 code and the new Tiny2350 code.

Closed 2024-09-05.

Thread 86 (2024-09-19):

src/pilomarcamera.py CalibrateFov fails AskYesNo() call

Short-bus, 2024-09-19:
When selecting Calibrate FOV option from the camera tools menu, the option fails because the function AskYesNo() is not found in src/pilomarcamera.py

CameraInUse.CalibrateFov()
NameError: name 'AskYesNo' is not defined

Short-bus, 2024-09-21:
Added missing AskYesNo() function definition.

Closed 2024-09-21.

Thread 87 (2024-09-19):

AutoPreview fails at Parameters.CameraAutoCommand reference

Short-bus, 2024-09-19:
The reference to Parameters.CameraAutoCommand is from an earlier version. The attribute is now Parameters._CameraAutoCommand
because it is a dynamically assigned parameter now.

Closed 2024-09-21.

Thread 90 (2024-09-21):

circuitpython/tiny2040/code.py is an HTML file.

Short-bus, 2024-09-21:
Message via Instructables website

`I took a snapshot of the GitHub repository on 31Aug24 after your new s/w release but did not install. I took a second snapshot today before I proceeded with the s/w rebuild and it looks like the Tiny2040 code.py file has got corrupted somewhere between these two dates. It's now an html type file.
`

Checked online and it is indeed downloading as an HTML file for some reason.
Needs replacing with Python original.

Closed 2024-09-21.

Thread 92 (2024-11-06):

Scaling

michael19101, 2024-11-06:
Hello,
I would like to scale up the observatory or create a larger design. I am aware that the number of teeth on the gears will change. Can this be corrected through software? How does the program calculate the positions of the stars and convert them into motor rotations? Another idea would be to control the telescope with a 3D printer board and operate it with a Raspberry Pi in headless mode via network (see OpenAstroTracker).

Best regards, Michael.

Short-bus, 2024-11-06:
Hi Michael,

Yes, the gearing, steps and direction can be adjusted through the parameters.
You can set different values there if you use a different design.
Also limited parameters to support slightly different stepper driver chips.
All the parameters are in the data/pilomar_params.json file. It's created with default values when you first start the program.

In the /docs folder there's a .pdf file with some extra information about the project, there's a section in there which briefly explains what each parameter is.
https://github.com/Short-bus/pilomar/blob/main/docs

Star positions are calculated using the Skyfield library. Pi-lomar has a catalog of stars, planets, galaxies etc. The Skyfield package allows these to be converted into realtime locations in the sky as 'altitude' (up/down) and 'azimuth' (left/right) angles. Those angles are then easy to convert into motor step positions. The software passes the step positions directly to the motorcontroller to act as a GOTO. The motorcontroller compares the requested step position with the current position and issues MOVE signals to the motors as required. During actual photography it passes a list of GOTO positions and timestamps that the motor must follow autonomously... that's the 'trajectory' that the telescope will use.

For example: In a 'default' build the physical gearing is a ratio of 240:1 and the motor stepping is a ratio of 400:1, giving an overall step to angle ratio of 96000:1. This means the telescope by default can move to 96000 different positions of azimuth, and 24000 positions of altitude. About 0.00375 degrees per motor step. You can increase this by choosing 1/2, 1/4 or 1/8 microstepping, but eventually you hit a maximum step signal speed that the microcontroller can deliver and things get slow. (It may be possible to do something smarter with PWM signals to improve this?)

If you're building a system with VERY fine movement then a 3D printer board may be worth investigating. There are some speed limitations with the Tiny2040 and CircuitPython, the new Tiny2350 microcontroller offers better performance, I recommend that.

Good luck with the design and build.
Matt.

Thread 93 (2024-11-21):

Loading MPC comet file CometEls.txt fails.

Short-bus, 2024-11-21:
From @HOPKIRS21

When I run the program it gives me the following output:

```
pilomar 1.1.0

/usr/local/lib/python3.11/dist-packages/pandas/core/arrays/masked.py:60: UserWarning: Pandas requires version '1.3.6' or newer of 'bottleneck' (version '1.3.5' currently installed).
from pandas.core import (
Hostname: Pilomar
Locale: ('en_US', 'UTF-8')
Using realtime clock.
Project root /home/*********/pilomar
Current time is: 2024-11-14 01:23:36.036666+00:00 UTC, offset is None seconds.
pilomar.py 2024-09-21 11:53:37
Main log to /home/*********/pilomar/log/pilomar_20241114012336.log
Camera log to /home/*********/pilomar/log/pilomar_camera_20241114012336.log
2024-11-14 01:23:36 RPi: Model: RPi 4 B 1.5 Num: 4 OStype: debian OSid: 12 OSname: bookworm OSbits: 64 OSproc: aarch64 SysKey: 4/bookworm/64
Removing out of date log files to preserve disc space...
find /home/*********/pilomar/log -type f -name 'pilomar_*.log' -mtime +2 -delete
Done.
2024-11-14 01:23:36 Loading parameters from file: /home/*********/pilomar/data/pilomar_params.json
Current UTC time is: 2024-11-14 01:23:36.090534+00:00
Local time is: 2024-11-13 20:23:36.090534-05:00
Python3 is UTF-8 compliant, make sure that the terminal is in UTF-8 mode too.
2024-11-14 01:23:36 Image storage: /
Camera enabled
2024-11-14 01:23:45 No recovery log file found for azimuth motor. Assuming 180.000°
2024-11-14 01:23:45 No recovery log file found for altitude motor. Assuming 000.000°
2024-11-14 01:23:45 Home location Latitude ********* N, Longitude ********* W
2024-11-14 01:23:45 Hipparcos data cache exists, using that.
2024-11-14 01:23:49 Loading Messier catalog from /home/*********/pilomar/data/messierobjects.json ...
2024-11-14 01:23:49 Loading constellation patterns...
2024-11-14 01:23:49 Loading New General Catalog (NGC) entries from /home/*********/pilomar/data/ngc.json ...
2024-11-14 01:23:49 NGC data cache exists, using that.
2024-11-14 01:23:49 Loading meteor shower list from /home/*********/pilomar/data/meteors.json ...
2024-11-14 01:23:49 Loading comet list from https://www.minorplanetcenter.net/iau/MPCORB/CometEls.txt ...
Traceback (most recent call last):
File "/home/*********/pilomar/src/pilomar.py", line 5112, in
comets = mpc.load_comets_dataframe(f) # Comet data loaded as a Pandas dataframe.
^^^^^^^^^^^^^^^^^^^^^^^^^^^^
File "/usr/local/lib/python3.11/dist-packages/skyfield/data/mpc.py", line 186, in load_comets_dataframe
df = pd.read_csv(io.BytesIO(text), header=None, names=_COMET_FAST_COLUMNS)
^^^^^^^^^^^^^^^^^^^^^^^^^^^^^^^^^^^^^^^^^^^^^^^^^^^^^^^^^^^^^^^^^^^^^
File "/usr/local/lib/python3.11/dist-packages/pandas/io/parsers/readers.py", line 1026, in read_csv
return _read(filepath_or_buffer, kwds)
^^^^^^^^^^^^^^^^^^^^^^^^^^^^^^^
File "/usr/local/lib/python3.11/dist-packages/pandas/io/parsers/readers.py", line 626, in _read
return parser.read(nrows)
^^^^^^^^^^^^^^^^^^
File "/usr/local/lib/python3.11/dist-packages/pandas/io/parsers/readers.py", line 1923, in read
) = self._engine.read( # type: ignore[attr-defined]
^^^^^^^^^^^^^^^^^^^^^^^^^^^^^^^^^^^^^^^^^^^^^^^^
File "/usr/local/lib/python3.11/dist-packages/pandas/io/parsers/c_parser_wrapper.py", line 234, in read
chunks = self._reader.read_low_memory(nrows)
^^^^^^^^^^^^^^^^^^^^^^^^^^^^^^^^^^^
File "parsers.pyx", line 838, in pandas._libs.parsers.TextReader.read_low_memory
File "parsers.pyx", line 905, in pandas._libs.parsers.TextReader._read_rows
File "parsers.pyx", line 874, in pandas._libs.parsers.TextReader._tokenize_rows
File "parsers.pyx", line 891, in pandas._libs.parsers.TextReader._check_tokenize_status
File "parsers.pyx", line 2061, in pandas._libs.parsers.raise_parser_error
pandas.errors.ParserError: Error tokenizing data. C error: Expected 12 fields in line 584, saw 13
```

With the help of my one professors, we were able to bypass this issue.
What we ended up changing was which column in the comet data was being used to sort them because there was an error in the reference column.
We changed it to perihelion_year and it seems to have solved the issue.
It may be possible that this would cause a problem later on, so if you have any other suggestions, I would love to hear them.

Short-bus, 2024-11-21:
So far have not been able to recreate the error. However the Pandas version reported in the program output looks quite old (1.3.5). I think the installation script would currently install something like 1.5.3. Not sure if that's related at this point, but it's the only unusual message in the program output before the program fails.
Package versions can be checked from the 'Miscellaneous tools' menu, select 'About system' and check the final few lines of the output.

```
2024-11-21 17:00:23 Program: pilomar
2024-11-21 17:00:23 Program version: 1.2.0
2024-11-21 17:00:23 Project root: /home/pi/pilomar
2024-11-21 17:00:23 Microcontroller program version: 1.1.0 (good)
2024-11-21 17:00:23 Acceptable microcontroller versions: ['1.0', '1.1']
2024-11-21 17:00:23 Python version: sys.version_info(major=3, minor=11, micro=2, releaselevel='final', serial=0)
2024-11-21 17:00:23 Skyfield version: (1, 45)
2024-11-21 17:00:23 Astroalign version: 2.4.1
2024-11-21 17:00:23 Numpy version: 1.24.2
2024-11-21 17:00:23 Pandas version: 1.5.3
```

Closed 2025-04-18.

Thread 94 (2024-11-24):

UnicodeEncodeError: 'latin-1' codec can't encode characters in position 19-89: ordinal not in range(256)

Short-bus, 2024-11-24:
This error appears if the Raspberry Pi does not have UTF-8 character set selected.

An example startup output...
```
Hostname: raspberrypi
Locale: ('en_US', 'ISO8859-1')
...
  File "/home/pi/pilomar/src/textcolor.py", line 409, in TextBox
    print(line)
UnicodeEncodeError: 'latin-1' codec can't encode characters in position 19-89: ordinal not in range(256)
```

Short-bus, 2024-11-24:
The clue is in the output 'Locale: ('en_US', 'ISO8859-1').
The second item should be 'UTF-8'. Pi-lomar expects a UTF-8 environment.
In this case the operating system configuration is incorrect.
This can be fixed via the Raspberry Pi Configuration utility.
Go to the _Localisation_ tab.
Select _Set Locale_.
Change the _Character Set_ to **UTF-8**
Accept [OK] the changes then reboot the RPi.

The detection and error message will be improved in the next pi-lomar release.

Short-bus, 2024-12-08:
Found that the main cause of failure are the special characters in the SYMBOLS dictionaries in src/pilomar.py and src/textcolor.py. These are the characters for linedrawing, arrows, degree symbol etc. If the program recognises that the locale character set is not UTF-8 it should be possible to select an alternative SYMBOLS dictionary which is restricted to 7bit ASCII characters only.

Short-bus, 2025-04-20:
Closed with 2025-04 release.

Closed 2025-04-20.

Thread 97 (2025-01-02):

libcamera-still saves strange image dimensions for .dng files

Short-bus, 2025-01-02:
The --raw option in libcamera-still saves a copy of the raw bayer data from the camera sensor as a .dng file.
When a .DNG file is transferred into a Windows computer the image dimensions appear to be wrong.
They show as 253 * 190 pixels rather than 4056 * 3040 pixels.
The data appears to be the full format 4056*3040 when processed in DSS image stacker.
However other utilities (UFRaw) and Windows itself show the image as a thumbnail 253*190.

Is this a feature or a problem?

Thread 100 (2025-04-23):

Dimension mismatch error during Tracking operation

Short-bus, 2025-04-23:
Error issued during TRACKING operations

`pilomarimage.CreateTargetZoneBuffer: Dimension mismatch: Zone 0 zone shape: (3040, 4) latest shape: (3040, 4064)`

The latest version (1.2.0 Apr.2025) uses a variable size master map.
If the LatestImage is larger than the MasterMap the array slicing receives a negative value which produces an incorrectly sized tracking zone map.

The error message appears if the following conditions are met
1) TrackingMapSpan parameter is the default 1.0
2) CameraDriver parameter is 'pilomarfits'

Workarounds
1) Increase TrackingMapSpan parameter to 1.1
OR
2) Change 'image types' to 'jpg & dng' which will switch from pilomarfits to libcamera.

Still investigating the detail, but initial study suggests the following

MasterMap dimensions are a multiple of the pixel size of the sensor (multiple is TrackingMapSpan parameter).
LatestImage is captured from the camera but can also be modified by the Tracking Filter mechanism.
The error only appears when LatestImage is generated by pilomarfits.py routine rather than libcamerastill.
- pilomarfits generates a slightly smaller image file due to the debayering mechanism in use.

Also: Spotted incorrect reference to a global variable in SetTargetImage() and CreateTargetZoneBuffer() methods of imagetracker class. Fixed in development but no effect on this particular issue.

Short-bus, 2025-04-24:
Fault appears to be in src/pilomarfits.py, the CCD matrix is 4064 bits wide. Looks like I was incorrectly keeping the extra 8 bits on each row of the JPG image in the final saved file. Only the first 4056 bits in each row are valid as the actual image.
Testing correction.

Closed 2025-04-28.

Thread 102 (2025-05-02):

False alarm for SPI being enabled in some builds

Short-bus, 2025-05-02:
The latest version checks if SPI and I2C are enabled to warn about config mistakes.
Got a report of one build which is returning a false error for SPI being enabled when it isn't.
The current check is just for 'spi_' kernel modules being loaded.
This may not be specific enough.

Current check is this

```
def spi_enabled(self):
    """ Return TRUE if SPI is enabled. """
    lines = osCmd('lsmod')
    result = False
    for line in lines:
        if 'spi_' in line:
            result = True
            break
    return result
```

May be more accurate to check for explicit modules.
Something like

```
def spi_enabled(self):
    """ Return TRUE if SPI is enabled.
        Looks for specific SPI kernel modules being loaded. """
    lines = osCmd('lsmod')
    result = False
    for line in lines:
        for entry in ['spi_bcm2708','spi_bcm2835']:
            if entry in line: # SPI kernel module is loaded.
                result = True
                break
    return result
```

Some more details of the exceptional builds needed to confirm this will be a good solution.

Workaround at the moment is to modify the spi_enabled() method to always return False

Short-bus, 2025-05-03:
Can recreate the situation if I disable SPI in raspi-config, but DON'T reboot the machine.
The spi kernel module stays loaded until rebooted.
Have added this to the error message if SPI is considered active as the program starts.

Closed 2025-05-03.

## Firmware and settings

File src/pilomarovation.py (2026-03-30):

# pilomarovation5.py
# CLASS for handling and rendering aurora ovation data from NOAA.

import numpy as np
import math
from pathlib import Path
import requests # To handle json response for seeing conditions from online services.
import json
from datetime import datetime, timedelta
import argparse

class pilomarovation():
    
    def __init__(self,obs_lat_deg=0,obs_lon_deg=0,width=256,height=128,shell_height_m=110e3,cache_seconds=1800):
        """
        handler for NOAA aurora ovation data.
        
        Imports data from the NOAA website.
        Creates a 'view' of the resulting aurora intensity from any given location on the Earth's surface.
        The resulting view can be exported in a few formats as required.
        
        The basis of this class was generated by AI.
        
        Parameters ----------------------------------------------------------
            obs_lat_deg (float) : Observer's latitude in degrees.
            obs_lon_deg (float) : Observer's longitude in degrees.
            width (int) : Unit width of output mapping. Often the image width in pixels or characters.
            height (int) : Unit height of output mapping. Often the image height in pixels or characters.
            shell_height_m (int) : How high is the aurora projection above the Earth's surface in metres.
            cache_seconds (int) : How many seconds can NOAA data be cached before refreshing from online.
        
        Usage ---------------------------------------------------------------
        
            # Dump view as CSV file.
            from pilomarovation import pilomarovation
            pa = pilomarovation(obs_lat_deg=53.68,obs_lon_deg=-93.40,width=256,height=128,shell_height_m=110e3) # Creat instance.
            pa.create_matrix_csv(filename='matrix.txt') # Write observer's view as text file matrix (csv)

            # Display view inline on the terminal.
            from pilomarovation import pilomarovation
            from textcolor import colordisplay
            pixel_width = 256
            pixel_height = 128
            char_width = int(pixel_width / 2)
            char_height = int(pixel_height / 4)
            pa = pilomarovation(obs_lat_deg=53.0,obs_lon_deg=10.5,width=pixel_width,height=pixel_height,shell_height_m=110e3) # Creat instance.
            pa.create_matrix_csv(filename='matrix.txt') # Write observer's view as text file matrix (csv)
            pa.create_ovation_csv(filename='ovation.txt') # Write ovation data (csv)
            pixellist = pa.get_matrix_list(above=True,below=True) 
            cd = colordisplay(rows=char_height,columns=char_width,name='ovation',fg=15,bg=0)
            cd.ListToBraillePlot(input_list=pixellist,threshold=0,fg=2,bg=0)
            cd.InlineDisplay()
        
        """
        self.AuroraURL = 'https://services.swpc.noaa.gov/json/ovation_aurora_latest.json' # Template for request URL.
        self.AuroraJSON = 'ovation_aurora_latest.json' # Filename on disc.
        self.RequestHeader = {"User-Agent": "Mozilla/5.0 (Windows NT 10.0; Win64; x64)"} # Websites often require headers submitting otherwise the request is denied.
        self.Online = True # Set to False if no web connection available.
        self.CacheMaxSeconds = cache_seconds # How many seconds old can the cache be? After that it needs refreshing.
        self.OutputWidth = width # 360 degree horizontal view is divided into this many points.
        self.OutputHeight = height # 180 degree vertical view is divided into this many points.
        self.IntensityDictionary = {} # Optimised dictionary of the intensity at each point in the shell.
        self.RawDictionary = {} # Raw JSON data from web.
        self.ShellHeight = shell_height_m # Height of shell above Earth surface (metres)
        self.ObserversLatDegree = obs_lat_deg
        self.ObserversLonDegree = obs_lon_deg
        self.ObserversLatRadians = np.radians(obs_lat_deg)
        self.ObserversLonRadians = np.radians(obs_lon_deg)
        self.AzGridRadians = None
        self.AltGridRadians = None
        self.OutputCellLat = None
        self.OutputCellLon = None
        self.AzDivisions = np.linspace(0, 360, self.OutputWidth, endpoint=False) # Create list of 'width' points from 0 to just under 360 evenly spaced.
        self.AltDivisions = np.linspace(-90, 90, self.OutputHeight) # Create list of 'height' points from -90 to 90 evenly spaced.
        self.DataTimestamp = None
        self.refresh() # Refresh data.

    def enu_to_ecef(self, e, n, u, lat0, lon0, h0):
        """
        Convert local ENU coordinates (e, n, u) to ECEF (x, y, z)
        relative to reference point (lat0, lon0, h0) (Observer).
        """
        # WGS84 constants
        a = 6378137.0
        e2 = 6.69437999014e-3

        # Convert reference point to radians
        lat0 = np.radians(lat0)
        lon0 = np.radians(lon0)

        # Compute prime vertical radius of curvature
        N0 = a / np.sqrt(1 - e2 * np.sin(lat0)**2)

        # Reference point in ECEF
        x0 = (N0 + h0) * np.cos(lat0) * np.cos(lon0)
        y0 = (N0 + h0) * np.cos(lat0) * np.sin(lon0)
        z0 = (N0 * (1 - e2) + h0) * np.sin(lat0)

        # Rotation matrix from ENU to ECEF (transpose of ECEF→ENU)
        R = np.array([
            [-np.sin(lon0), -np.sin(lat0)*np.cos(lon0),  np.cos(lat0)*np.cos(lon0)],
            [ np.cos(lon0), -np.sin(lat0)*np.sin(lon0),  np.cos(lat0)*np.sin(lon0)],
            [           0,  np.cos(lat0),               np.sin(lat0)]
        ])

        # Apply rotation
        dx, dy, dz = R @ np.array([e, n, u])

        return x0 + dx, y0 + dy, z0 + dz

    def ecef_to_enu(self, x, y, z, lat0, lon0, h0):
        """
        Convert ECEF coordinates (x, y, z) to local ENU coordinates
        relative to a reference point (lat0, lon0, h0) (Observer).
        All angles in degrees, all distances in meters.
        """
        # WGS84 constants
        a = 6378137.0
        e2 = 6.69437999014e-3

        # Convert reference point to radians
        lat0 = np.radians(lat0)
        lon0 = np.radians(lon0)

        # Compute prime vertical radius of curvature
        N0 = a / np.sqrt(1 - e2 * np.sin(lat0)**2)

        # Reference point in ECEF
        x0 = (N0 + h0) * np.cos(lat0) * np.cos(lon0)
        y0 = (N0 + h0) * np.cos(lat0) * np.sin(lon0)
        z0 = (N0 * (1 - e2) + h0) * np.sin(lat0)

        # Vector from reference to point
        dx = x - x0
        dy = y - y0
        dz = z - z0

        # Rotation matrix from ECEF to ENU
        R = np.array([
            [-np.sin(lon0),              np.cos(lon0),               0],
            [-np.sin(lat0)*np.cos(lon0), -np.sin(lat0)*np.sin(lon0), np.cos(lat0)],
            [ np.cos(lat0)*np.cos(lon0),  np.cos(lat0)*np.sin(lon0), np.sin(lat0)]
        ])

        # Apply rotation
        enu = R @ np.array([dx, dy, dz])
        return enu[0], enu[1], enu[2]

    def latlon_to_ecef(self,lat, lon, r):
        """
        Observer position in EARTH CENTRED, EARTH FIXED reference.
        ECEF is a Cartesian coordinate system with three perpendicular axes:
        Origin: the center of mass of the Earth
        X axis: points toward 0° longitude (intersection of equator and Greenwich meridian)
        Y axis: points toward 90°E longitude (equator, east of Greenwich)
        Z axis: points toward the North Pole
        So an ECEF position is simply: (x,y,z)    

        Parameters ------------------------------------------------
        lat (float) : Observer's latitude in radians.
        lon (float) : Observer's longitude in radians.
        r (float) : Radius of the Earth.
        
        Returns ---------------------------------------------------        
        numpy array : [x,y,z] position in cartesian space.
        """
        x = r * np.cos(lat) * np.cos(lon)
        y = r * np.cos(lat) * np.sin(lon)
        z = r * np.sin(lat)
        return np.array([x, y, z])

    def altaz_array_to_aurora_latlon(self):
        """
        Vectorized conversion of arrays of alt/az values into
        geographic lat/lon on the auroral shell.

        alt_deg_array and az_deg_array must be NumPy arrays
        of the same shape (e.g., 512x1024).

        Parameters -----------------------------------------------

        Returns --------------------------------------------------
        lat (array of float) : List of aurora shell latitudes for each altitude angle the observer wants to look at.
        lon (array of float) : List of aurora shell longitudes for each azimuth angle the observer wants to look at.

        """

        # ---------------------------------------------------------
        # 1. Constants
        # ---------------------------------------------------------
        R_EARTH = 6371e3
        R_SHELL = R_EARTH + self.ShellHeight

        # ---------------------------------------------------------
        # 2. Observer position in ECEF
        # ---------------------------------------------------------
        O = self.latlon_to_ecef(self.ObserversLatRadians, self.ObserversLonRadians, R_EARTH)  # shape (3,)

        # ---------------------------------------------------------
        # 3. ENU basis vectors (ECEF components)
        # ---------------------------------------------------------
        slat, clat = np.sin(self.ObserversLatRadians), np.cos(self.ObserversLatRadians)
        slon, clon = np.sin(self.ObserversLonRadians), np.cos(self.ObserversLonRadians)

        E_hat = np.array([-slon,  clon, 0.0])
        N_hat = np.array([-slat*clon, -slat*slon, clat])
        U_hat = np.array([ clat*clon,  clat*slon, slat])

        # ---------------------------------------------------------
        # 4. Convert alt/az arrays → ENU direction components
        # ---------------------------------------------------------
        ca, sa = np.cos(self.AltGridRadians), np.sin(self.AltGridRadians)
        caz, saz = np.cos(self.AzGridRadians), np.sin(self.AzGridRadians)

        # az measured from North toward East
        # ENU = EAST, NORTH, UP.
        e = ca * saz
        n = ca * caz
        u = sa

        # ---------------------------------------------------------
        # 5. Convert ENU → ECEF for all rays
        # ---------------------------------------------------------
        # d has shape (..., 3)
        d = (
            e[..., None] * E_hat +
            n[..., None] * N_hat +
            u[..., None] * U_hat
        )

        # Normalize all direction vectors
        d /= np.linalg.norm(d, axis=-1, keepdims=True)

        # ---------------------------------------------------------
        # 6. Ray–sphere intersection (vectorized)
        # ---------------------------------------------------------
        # Per-ray dot product O·d: broadcast O over all pixels
        Odotd = np.sum(O * d, axis=-1)      # shape (...,)
        O2 = np.dot(O, O)

        a = 1.0
        b = 2.0 * Odotd
        c = O2 - R_SHELL**2

        disc = b*b - 4*a*c
        mask = disc < 0  # rays that miss the shell

        sqrt_disc = np.sqrt(np.maximum(disc, 0.0))

        t1 = (-b - sqrt_disc) / 2.0
        t2 = (-b + sqrt_disc) / 2.0

        # Choose the positive intersection
        t = np.where(t1 > 0, t1, t2)
        t = np.where(t > 0, t, np.nan)  # mark invalid rays

        # Intersection points in ECEF, shape (..., 3)
        P = O + d * t[..., None]

        # ---------------------------------------------------------
        # 7. Convert intersection → lat/lon
        # ---------------------------------------------------------
        x, y, z = P[..., 0], P[..., 1], P[..., 2]
        r = np.sqrt(x*x + y*y + z*z)

        lat = np.degrees(np.arcsin(z / r))
        lon = np.degrees(np.arctan2(y, x))

        # Mask invalid rays
        lat[mask] = np.nan
        lon[mask] = np.nan

        # Height is inverted, so flip the arrays
        lat = np.flipud(lat)
        lon = np.flipud(lon)
        
        lon = lon % 360 # Convert from -179<>179 to 0<>359 range.
        
        self.OutputCellLat = lat
        self.OutputCellLon = lon

        return True

    def build_grid(self):
        """ 
        Construct a couple of arrays in the dimensions of the output data giving the observer's azimuth and altitude that each 
        output cell represents. These are used to map to the correct cells in the aurora intensity data that is 
        projected into the shell above the observer. 
        
        Parameters -------------------------------------
        
        Returns ----------------------------------------
        az_grid is a repeating list of all azimuth positions. Each row contains all positions, as many rows as alt containts.
        alt_grid is a matching matrix of altitude positions. Each row represents a single alt value, but repeated for all az positions.
        
        """
        # Build a grid of alt/az values
        # self.AzDivisions = np.linspace(0, 360, self.OutputWidth, endpoint=False) # Create list of 'width' points from 0 to just under 360 evenly spaced.
        # self.AltDivisions = np.linspace(-90, 90, self.OutputHeight) # Create list of 'height' points from -90 to 90 evenly spaced.

        az_grid, alt_grid = np.meshgrid(self.AzDivisions, self.AltDivisions) # Create a matrices of all the point combinations.
        # az_grid is a repeating list of all azimuth positions. Each row contains all positions, as many rows as alt containts.
        # alt_grid is a matching matrix of altitude positions. Each row represents a single alt value, but repeated for all az positions.
        
        self.AzGridRadians = np.radians(az_grid)
        self.AltGridRadians = np.radians(alt_grid)
        
        return True
        
    def get_shell_map(self,flip=False):
        """
        Return a list of output cells and the corresponding lat/lon coordinates in the aurora shell.
        List is a list of rows, each row is a list of columns, each entry is a tuple of (lat/lon) on the aurora shell.
        """
        result = []
        for direction_alt in range(self.OutputHeight): # What direction (altitude) are we looking at?
            line = []
            for direction_az in range(self.OutputWidth): # What direction (azimuth) are we looking at?
                shell_lat = int(self.OutputCellLat[direction_alt,direction_az]) # What latitude in the 'shell' are we looking at?
                shell_lon = int(self.OutputCellLon[direction_alt,direction_az]) # What longitude in the 'shell' are we looking at?
                # What's the 'shell' intensity at that point?
                location = (int(shell_lat),int(shell_lon)) # Construct key to dictionary to retrieve intensity at that point. (lat,lon)
                line.append(location)
            result.append(line)
        if flip: result.reverse() # Invert rows
        return result

    def cache_needs_updating(self):
        """ 
        Return False if disc cache can be used. 
        Return True if it needs refreshing from the web. 
        """
        download = self.Online # Set to TRUE to download a fresh copy of the data, FALSE if you can use the disc cache.
        path = Path(self.AuroraJSON) # This is where the disc cache file should be.
        if path.is_file(): # File exists.
            creation_time = datetime.fromtimestamp(path.stat().st_ctime)
            temp = (datetime.now() - creation_time).total_seconds()
            #print("pilomarovation():",self.AuroraJSON,"is",temp,"seconds old.")
            if temp < self.CacheMaxSeconds: # File is young enough.
                download = False # Don't need an online refresh.
        return download
        
    def construct_intensity_dictionary(self):
        """
        Optimise intensity dictionary.
        Takes the raw JSON data received from the web service.
        Creates an indexable dictionary for each lat/lon square with the aurora intensity at that point.
        """
        self.IntensityDictionary = {}
        for ilon,ilat,intensity in self.RawDictionary['coordinates']:
            location = (int(ilat),int(ilon)) # (lat,lon)
            intensity = int(intensity)
            self.IntensityDictionary[location] = intensity
        return True
    
    #def downscale_matrix_list(self, grid, new_rows, new_cols):
    #    """
    #    Produce new matrix_list which is a scaled down version of the full list.
    #    
    #    Parameters ------------------------------------------------
    #    grid (list) : Original copy of matrix list that should be compressed.
    #    new_rows (int) : Reduced number of rows to compress into.
    #    new_cols (int) : Reduced number of columns to compress into.
    #    """
    #    old_rows = len(grid)
    #    old_cols = len(grid[0])
    #
    #    row_scale = old_rows / new_rows
    #    col_scale = old_cols / new_cols
    #
    #    result = []
    #
    #    for r in range(new_rows):
    #        row_start = int(math.floor(r * row_scale))
    #        row_end   = int(math.floor((r + 1) * row_scale))
    #        row_end   = min(row_end, old_rows)
    #
    #        new_row = []
    #        for c in range(new_cols):
    #            col_start = int(math.floor(c * col_scale))
    #            col_end   = int(math.floor((c + 1) * col_scale))
    #            col_end   = min(col_end, old_cols)
    #
    #            # Compute max over the block
    #            block_max = max(
    #                grid[rr][cc]
    #                for rr in range(row_start, row_end)
    #                for cc in range(col_start, col_end)
    #            )
    #
    #            new_row.append(block_max)
    #
    #        result.append(new_row)
    #
    #    return result
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

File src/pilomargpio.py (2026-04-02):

#!/usr/bin/python

# Raspberry Pi GPIO library.
# Presents an interface to the GPIO handlers on the Raspberry Pi SBCs.
# - Different classes can be built to handle different GPIO handlers, 
#   but all should present the same interface to the calling programs.

# Mar.2026: GPIOD library has changed between BOOKWORM and TRIXIE.
#           A temporary 'shim' has been added to maintain compatibility between the two versions.
#           This is pending a rewrite of the GPIO handlers for both BOOKWORM and TRIXIE.

# This software is published under the GNU General Public License v3.0.
# Also respect any pre-existing terms of any components that this incorporates.

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
class gpio_opt():
    """ Constants. """
    GPIO_DRIVER = 'GPIO' # Buster
    GPIOD_DRIVER = 'GPIOD' # Bookworm

GPIO_DRIVER = None
try:
    import RPi.GPIO as GPIO # Handling IO signals. If available.
    GPIO.setmode(GPIO.BCM)
    GPIO_DRIVER = gpio_opt.GPIO_DRIVER # "GPIO"
except: # No support for RPi.GPIO detected.
    try:
        import gpiod # Handling IO signals. If available.
        #import compat_gpiod as gpiod # This is a compatibility wrapper for GPIOD while this code transitions from V1 to V2 GPIOD
        _ = hasattr(chip, "get_line") # If on Trixie the bindings are broken for GPIOD so we need a different solution.
        GPIO_DRIVER = gpio_opt.GPIOD_DRIVER # "GPIOD"
    except: # No support for GPIOD detected.
        try:
            import gpiod_trixie as gpiod # Shim to simulate GPIOD via LIBGPIOD. Original GPIOD bindings are broken in Trixie. 
            GPIO_DRIVER = gpio_opt.GPIOD_DRIVER # "GPIOD"
        except: # No support for GPIOD detected.
            pass
    
if GPIO_DRIVER == gpio_opt.GPIOD_DRIVER: # 'GPIOD': # Select the GPIO handling chip.
    success = False
    chip_list = ['gpiochip4','gpiochip0','/dev/gpiochip0']
                 # gpiochip4 early BOOKWORM
                 # gpiochip0 late BOOKWORM
                 # /dev/gpiochip0 TRIXIE
    for chip in chip_list:
        try:
            GPIOchip = gpiod.Chip(chip)
            success = True
            print("Selected GPIOD chip:",chip)
            break
        except Exception as e:
            print(str(e))
            print("Rejected GPIOD chip:",chip,"Trying another")
    if not success:
        print("GPIOD: Unable to select a valid chip from",chip_list)
        exit()

def cleanup_gpio():
    """ Perform cleanup at end of session. """
    GPIO.cleanup()

class inputpin_gpio():
    """ Wrapper for GPIO input pin. 
        Allows different GPIO libraries to be implemented by hiding the actual implementation behind these methods. 
        Pin can be declared as None in which case it's a non-functional device. """
    
    InputPins = [] # List of all defined input pins.
    __library__ = 'RPi.GPIO' # Which GPIO library does this support?
    __version__ = '0.1.1' # What version of the library is this?
    
    def __init__(self,pinbcm,name=None,pull="up",enabled=True,invert=False):
        """ Define a GPIO input pin.
        
            The purpose is to present a common interface to an I/O pin regardless of the underlying
            GPIO package being used. You can create alternative classes which interact with different 
            packages and present the same interface to the program.
        
            pinbcm = the BCM pin number. 
            name is an optional name for the pin. 
            pull = GPIO.PUD_UP for pull up (default HIGH/ON), 
                   GPIO.PUD_DOWN for pull down. (default LOW/OFF)
            enabled = initial enabled(True)/disabled(False) state of the pin.
            invert = False: IsOn returns TRUE for HIGH signal. 
                            IsOff returns TRUE for a LOW signal.
                     True:  IsOn returns TRUE for LOW signal.
                            IsOff returns TRUE for a HIGH signal.
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

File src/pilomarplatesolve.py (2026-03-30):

# astrometry.net platesolver code.

"""
platesolve.py

Minimal, self-contained wrapper around astrometry.net's `solve-field`
for use on a Raspberry Pi with the HQ camera.

- No external Python deps beyond the standard library
- Uses `solve-field` installed on the system
- Parses the generated .wcs file to extract basic WCS info

Tested conceptually for wide-field lenses (e.g. 16mm, 50mm on IMX477).

Requires that pilomar project is installed.
Requires that astrometry.net is installed.
Requires that astrometry.net data files are installed.

sudo apt update
sudo apt upgrade
sudo apt install astrometry.net
sudo apt install astrometry-data-2mass-08-19
#sudo apt install astrometry-data-4206 astrometry-data-4207 astrometry-data-4208 \
#                 astrometry-data-4209 astrometry-data-4210 astrometry-data-4211 \
#                 astrometry-data-4212

"""

from pathlib import Path
#from typing import Optional, Dict
from pilomarlib import IsFloat,IsInt,TextToInt,TextToFloat,attributemaster # Import some helper classes.
from pilomaroscommand import oscommand # Pilomar's OS command executor.
from astropy.io import fits 
from pilomarimage import pilomarimage
from datetime import datetime, timedelta 
from pilomartrig import AngleToHMS, AngleToDMS
import math 
import numpy as np
import pandas 
import json

class PlateSolver(attributemaster):
    """
    Wrapper for astrometry.net library to perform platesolving on images captured by pilomar telescope.
    """

    def __init__(self,name,logger=None,pilomarsession=None,projectroot=None,parameterfile=None,filter_script='PrepForPlateSolving',script_source=None,debug=False):
        """
        Create instance of PlateSolver
        
        Parameters --------------------------------------
        name (str) : Name for the instance. (For debugging messages)
        logger (pilomarlog instance) : optional: Links to a pilomar logging mechanism.
        pilomarsession (pilomarsession instance) : optional : Links to a pilomarsession instance.
        projectroot (str) : Path to pilomar project root folder (ie '/home/pi/pilomar/')
        parameterfile (str) : Path to parameter file. Default will be assumed if not set.
        filterscript (str) : Name of pilomarimage filter to use for cleaning images. (Default is used if not set.)
        """
        self.Name = name 
        self.SetLogger(logger) # Inherited from attributemaster
        if projectroot == None:
            self.ProjectRoot = '/home/pi/pilomar' # Root of the pilomar project, can be changed at runtime or when instantiated.
        else:
            self.ProjectRoot = projectroot # Root of the pilomar project, can be changed at runtime or when instantiated.
        if parameterfile != None: self.ParameterFileName = parameterfile
        else: self.ParameterFileName = self.ProjectRoot + '/data/pilomar_params.json'
        self.TempDir = self.ProjectRoot + '/temp/' # Where are temporary files stored?
        self.FilterScript = filter_script # Name of PilomarImage filterscript to execute.
        self.ScriptSource = script_source # File containing filter scripts (uses pilomarimage defaults if missing).
        self.HipparcosCacheFile = self.ProjectRoot + '/data/hipparcos.pkl' 
        self.Session = pilomarsession # Link to parent session instance (Gives access to everything else in the session)
        self.OSCommand = oscommand(logger=logger) # Create OS Command executor. Pass handle to the 'log' method.
        self.osCmd = self.OSCommand.Execute # Shortcut point to the execution method which returns the output.
        self.osCmdCode = self.OSCommand.ExecuteCode # Shortcut point to the execution method which returns the termination code.
        self.DebugMode = debug # Activate additional development/debugging features.
        # Create and load PilomarParameters dictionary.
        self.ReadParameterFile(self.ParameterFileName)
        self.Reset()
        
    def Reset(self):
        """
        Reset any image and solution.
        """
        self.SolutionDict = {} # Processed dictionary of solution details.
        self.FitsHeader = {} # Intermediate dictionary of details from solver's FITS header.
        self.StarCount = 0 # How many stars in image.
        self.StarList = [] # x,y,r of each identified star.
        self.IdentityList = [] # Calculate list of RADEC locations based upon StarList.        
        self.HipparcosDf = None # Pandas dataframe of Hipparcos catalog.
        self.Image = None # Pilomarimage instance for the image being processed.
        self.OrigImageFile = None # The original image file on disc.
        self.ExifData = {} # No EXIF data loaded.
        self.SolveSeconds = 0 # Elapsed seconds for calculating the solution.

    def LoadHipparcosDf(self):    
        """
        Hipparcos catalog is loaded as Pandas dataframe. 
        The file is loaded from disc (self.HipparcosCacheFile), it is installed as part of the pilomar installation.
        """
        if self.HipparcosDf is None:
            self.HipparcosDf = pandas.read_pickle(self.HipparcosCacheFile)
            self.HipparcosDf["ra_rad"] = np.radians(self.HipparcosDf["ra_degrees"]) 
            self.HipparcosDf["dec_rad"] = np.radians(self.HipparcosDf["dec_degrees"]) 
            self.HipparcosDf["cos_dec"] = np.cos(self.HipparcosDf["dec_rad"])            
        self.Log("Hipparcos dataframe loaded",len(self.HipparcosDf),"stars from cache.",terminal=False)
        self.Log("Hipparcos dataframe contains",list(self.HipparcosDf.columns),"columns.",terminal=False)
        return True

    def NearestStar(self, ra_deg, dec_deg):
        """
        Return dictionary of the nearest star from the Hipparcos dictionary to any RADEC coordinates.
        """
        # Convert query point to radians
        ra_q  = np.radians(ra_deg)
        dec_q = np.radians(dec_deg)

        # Differences
        dra  = self.HipparcosDf["ra_rad"].values  - ra_q
        ddec = self.HipparcosDf["dec_rad"].values - dec_q

        # Small-angle spherical distance
        dist = np.sqrt((dra * np.cos(dec_q))**2 + ddec**2)

        # Index of closest star
        idx = np.argmin(dist)

        row = self.HipparcosDf.iloc[idx]
        return {
            "hip": row.hip,
            "name": row.label,
            "starname": row.starname,
            "distance_rad": dist[idx],
            "ra_degrees": row.ra_degrees,
            "dec_degrees": row.dec_degrees,
        }
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

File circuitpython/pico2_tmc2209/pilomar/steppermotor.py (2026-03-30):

# pilomar/steppermotor.py - Circuitpython 9.2 build for Raspberry Pi Pico 2 (RP2350).
# For use with Raspberry Pi Pico 2 only.
# Dec.2024 / Refactored with help from TPROFFEN.
# May.2025 / Now exclusively Pico2 code version.

#-----------------------------------------------------------------------------------------------

steppermotor_version = "0.0.1" # A version number for this source code.

#-----------------------------------------------------------------------------------------------

from pilomar.helpers import * # Utility classes and methods used in this program. (logfile, clock, gpio etc)
print('pilomar.helpers:',helpers_version) # Print source code version number.
from pilomar.trajectory import * # Trajectory handling classes and methods used in this program. (trajectorypoint and trajectory)
print('pilomar.trajectory:',trajectory_version) # Print source code version number.
import tmc2209
import time 

class steppermotor():
    
    motor_list = [] # List of globally defined motors. 
    
    """ Handler for a NEMA17 stepper motor with TMC2209 driver chip. """
    def __init__(self,name,logfile,clock,exceptioncounter,features,TMCuart,motor_id,rpi,vmot,statusled):
        """ Create new instance of steppermotor class. 
            The motor still needs to be configured once created.
            
            Parameters ---------------------------------------------------------------------
            name : A name for the motor. Eg 'altitude'. 
            logfile : Handle to LogFile instance for logging messages. 
            clock : Handle to Clock instance for time functionality. 
            exceptioncounter : Handle to ExceptionCounter instance for error notification. 
            features : List of system features. 
            TMCuart : Handle to TMC2209 UART handler for this motor. 
            motor_id : Integer number. Unique ID number for this motor, must match ID wiring of the TMC2209 chip.
            rpi : Handle to UART comms for RPi.
            statusled : Handle to statusled instance. """
        self.MotorName = name
        self.LogFile = logfile # Instance of LogFile class.
        self.Log = logfile.Log # Instance of Log method of LogFile class.
        self.RPi = rpi # Instance of uarthost class.
        self.VMot = vmot # Link to VMot() function to check motor supply.
        self.Clock = clock # Instance of clock class.
        self.ExceptionCounter = exceptioncounter # Instance of ExceptionCounter class.
        self.StatusLed = statusled # Instance of statusled class.
        self.Features = features
        self.MotorID = motor_id
        # Define attributes here which will NOT be 'reset'.
        #self.as5600 = None # Instance of as5600_handler class. Link to any as5600 sensor handler connected to this axis.
        self.tmc2209 = None # Link to tmc2209 handler instance. Initialised below...
        self.position_sensor = None # Instance of a position sensor. API must have standard signature.
        #self.lis3dh = None # Instance of lis3dh_handler class. Link to LIS3DH accelerometer instance.
        # Set up control pins for the motor.
        # If we're using the same pins to drive multiple motors you may get some warnings from GPIO.
        # If the program has been restarted in the same session, you may get some warnings from GPIO.
        self.StepBCM = None # OUTPUT: This sends the MOVE pulse to the controller.
        self.DirectionBCM = None # OUTPUT: This sets the MOVE direction to the controller.
        self.EnableBCM = None # OUTPUT: This enables/disabled the motor.
        self.FaultBCM = None # INPUT: Will EARTH when triggered.
        self.PulseEndNs = 0 # time.monotonic_ns() value when a step pulse should end.
        self.PulseStartNs = 0 # time.monotonic_ns() value when self.PulseEndNs was set (used to detect clock resets)
        # Define attributes that WILL be 'reset' here.
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

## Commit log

2023-02-01 Update textcolor.py
    printing to a scrolling window can now specify overriding color scheme
2023-05-03 Initial version of code.py
    circuitpython routine to run on Pimoroni Tiny2040 microcontroller.
    This communicates via UART with the Raspberry Pi.
    The microcontroller sits on the motorcontrol circuitboard and directs the motors to follow instructions and trajectories provided by the Raspberry Pi.
2023-05-04 Moved some classes into include files
    Moved CPUMONITOR, DISCMONITOR, MEMORYMONITOR, LOGFILE, OSCOMMAND and TIMER classes into separate include files.
    Starting to modularize the code where possible.
2023-10-31 Summer2023 changes
    New version of code.py circuitpython microcontroller code.
    Multiple improvements to message handling and more reliability for movement routines.
2023-11-29 Fixed MotorRunningSeconds and outdated ncg.json
    Fixes 2 issues with the published version.
    1)(a) MotorRunningSeconds was referenced in the recovery file, but does not exist in this version of the motorcontrol class. Now removed.
    1)(b) Writing to recovery file now tries maximum 100 times before erroring out.
    2) MarkupPreview failed to mark ngc items if the njc.json file was an older format. Program now tolerates this, and the njc.json file has been updated too.
2023-12-18 #40 UART TX overflow when ignoring DRV8825 fault.
    Resolves issue #40 where the UART TX buffer fills and causes the program to crash if DRV8825 raises a FAULT signal, code.py is set to ignore it.
    New version only sends a single comment to the RPi instead of one comment per motor step.
    [code.py]
2023-12-18 Fix issues 34,35,37,38,39
    #34 Add parameters for star selection magnitude for star lists.
    #35 Check ProjectPath variable is respected globally.
    #37 Relax the version cross-check between pilomar.py and code.py programs.
    #38 MaxAltitudeAngle parameter shows as 360Degrees rather than 90Degrees.
    #39 After building the Hipparcos star catalog, pilomar terminates at target prompt.
    [pilomarcelestrak.py]
2023-12-30 #45 Tiny2040 ADC0 pin can be reallocated.
    There is now a switch to define the mode of the ADC0 pin on the Tiny2040.
    This was originally used to measure the power voltage to the stepper motors.
    New PCB designs no longer require that measurement so the pin is free for other purposes.
    A flag in the software now lets you turn the ADC measure on/off for that pin.
    [code.py]
2023-12-30 Final Dec-2023 copies of RPi software.
    Tested copies of the software for the Raspberry Pi side with Dec-2023 issues completed.
    [pilomarlogfile.py]
2023-12-31 pilomarlogfile.py corrected reference to NowUTC()
    pilomarlogfile.py ZipCommsLog() had reference to wrong NowUTC() method, correct version now committed.
    [pilomarlogfile.py]
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2024-01-03 Gerber files to produce the motorcontroller PCB
    These files can be used to manufacture the unpopulated PCB for pi-lomar's motorcontroller.
    [Drill_NPTH_Through.DRL, Drill_PTH_Through.DRL, Drill_PTH_Through_Via.DRL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]
2024-01-14 Testing Efficient Move logic
    This is the version in test which nolonger forces the telescope to 'wind back' rotating the long way around for some moves.
    This version has a switchable feature which allows the telescope to select the shortest path between two positions.
    Default behaviour is to retain the original functionality.
    New behaviour can be triggered by setting the new parameter OptimiseMoves = True in the parameter file.
    This requires matching update to pilomar.py in this branch.
    [code.py]
2024-01-14 Supports new OptimiseMoves parameter
    This is to support new optimised move feature in circuitpython/code.py
    New parameter OptimiseMoves = False by default to retain previous functionality (Telescope will not pass through Due North, but 'unwinds' from 359Deg to 0Deg).
    When True the microcontroller logic is free to use the shortest path between two positions, even passing through Due North if needed.
2024-01-31 Manual updated with an example observation
    Added a section at the end of the draft manual to include an example observation, samples of various images and explanations of what is happening.
    Example added this time was M42 Orion Nebula taken in challenging misty/light polluted skies using infrared sensitive sensor - still able to capture interesting details that you would not see with th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
2024-02-08 Updates from final round of testing
    Final round of testing for this release.
    Also includes streamlined microstepping support.
    src/pilomar.py and circuitpython/code.py now get motor configurations from common source.
    Configurations now in parameter file rather than hardcoded.
2024-02-22 O/S specific build scripts
    The build scripts for buster 32bit and bookworm 64bit are different.
    The original buildpilomar script is now available as two versions.
    buildpilomar_bookworm64 will build pilomar on Bookworm 64bit.
    buildpilomar_buster32 will build pilomar on Buster 32bit.
    The original buildpilomar script still exists, and is the same as the buster 32bit script.
    To build on a Raspberry Pi 3B - use buildpilomar_buster32
    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
2024-02-22 Initial support for Bookworm 64bit
    First version of support for bookworm 64bit O/S on Raspberry Pi 4B only.
2024-02-25 Fixed line terminators in script
    buildpilomar_bookworm64 had DOS terminators on the lines.
    Switched back to LINUX terminators.
2024-05-10 Work in progress
    Snapshot of current development.
    Main development in this snapshot is the introduction of pilomarfits.py to generate basic .fits image files from the bayer raw data.
2024-07-03 June/July updates.
    Improved image type selection.
    Added microstepping configuration options to motor menu to simplify setting up microstepping.
2024-07-03 Jun/Jul updates
    Older scripts now adapt to the raspberry pi user name.
    Earlier versions always assumed the 'pi' user.
2024-07-10 metadata capture nolonger needs separate exposure
    Previous version of the library performed a separate exposure to capture camera metadata.
    Re-reading the picamera2 library revealed that it can be extracted as part of the primary image capture too.
    Code reworked to do this, which speeds up the cycle time for image capture.
    Metadata is stored as .json file in same directory as the images.
    Still only works when saving FITS files at the moment.
    You need to add the '--metadata' option to the pilomarfits 'light' image command template in the parameter file.
    [pilomarfits.py]
2024-07-10 ChooseLens added to Camera Tools menu
    Menu options now available to choose between 16mm and 50mm lens.
    This sets the parameter file values appropriately for each lens size.
    You still need to restart the program after making the selection so that the new values propagate fully.
2024-09-02 Create README.txt
    Copy of code.py that runs on the Pimoroni Tiny2350.
    Has higher capacity than previous Tiny2040.
2024-09-02 Rearrange file locations
    Moved original code.py for Tiny2040 from /circuitpython to /circuitpython/tiny2040 folder. No code changes from previously released version.
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2024-09-02 code.py for Pimoroni Tiny2350 circuitpython 9.2
    Added initial version of code.py for Pimoroni Tiny 2350 microcontroller.
    Expects circuitpython 9.2 - use the uf2 file specifically for the Tiny2350 so that all GPIO pins operate as expected.
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2024-09-05 ADC0 pin is unassigned by default
    Tiny2350 returns the option to use ADC0 as a voltage measure for the motor input voltage.
    Enable it by removing the '#' from
    # FEATURES.append('VMOT') # This turns the free ADC0 pin on the Tiny into a measure of motor power voltage.
    You need to provide an appropriate circuit with a voltage divider to measure the voltage safely.
2024-09-11 GPIOD support for gpiochip0 and gpiochip4
    On RPi5 Bookworm recent builds the GPIOD library can fail if the O/S has assigned the GPIO chip to 'gpiochip0' instead of the original 'gpiochip4'.
    If 'gpiochip4' fails, this will fall back to 'gpiochip0'.
    [pilomargpio.py]
2024-09-21 Added missing AskYesNo function definition
    AskYesNo() function calls failed because function was not defined in the code. Have copied the definition into pilomarcamera.py from pilomar.py
    [pilomarcamera.py]
2024-09-21 Corrected Parameters._CameraAutoCommand reference
    AutoPreview included an out of date reference to Parameters.CameraAutoCommand.
    Now corrected to Parameters._CameraAutoCommand.
2024-11-29 Added simple guide to motorcontroller wiring
    This documents explains in simple terms how to build the motorcontroller circuit.
    It covers
    - Wiring the RPi to the Microcontroller.
    - Wiring the Microcontroller to the MotorDrivers.
    - Wiring the MotorDrivers to the Motors.
    Included as it may be useful for troubleshooting circuit designs.
2025-04-18 Added default datafiles.
    Some online resources for datafiles are not always available.
    Have added a default copy of de421.bsp (planet orbit data) and constellationship.fab (constellation patterns) into the repository in case the online sources are unavailable.
    It's possible that both these have changed location or format. So these archived copies will keep the current software version happy.
2025-04-28 Fix issue 100: Dimension mismatch during tracking operation
    This fixes issue #100
    pilomarfits.py now saves the correctly dimensioned .jpg images.
    It was including the extra pixels at the end of each row of the sensor, it now only saves the active image area.
    [pilomarfits.py]
2025-04-28 Update pilomarfits.py
    Updated minor release version because of fix to Issue100
    [pilomarfits.py]
2025-05-03 Fix issue 102: False alarm for SPI being enabled.
    Addresses issue #102.
    If SPI is disabled via raspi-config but the computer is not rebooted, the kernel module remains loaded.
    The program now checks for more specific SPI module names, and also issues a warning that a reboot my be required if the module is still loaded.
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2026-03-30 Library fixes after testing.
    Various fixes to libraries pending the release of the next version of the main program.
    [pilomarlogfile.py, pilomarmetcheck.py, pilomarovation.py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]
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2026-04-02 Trixie GPIOD workaround
    GPIOD library adjusted further to maintain support under Trixie.
    pilomargpio.py uses different GPIO handler in each O/S but presents a common interface to the program.
    - Trixie uses gpiod_trixie which implements Bookworm GPIOD library calls for new libgpiod structure.
    - Bookworm uses gpiod library as before.
    - Buster uses gpio library as before.
    [gpiod_trixie.py, pilomargpio.py]
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
